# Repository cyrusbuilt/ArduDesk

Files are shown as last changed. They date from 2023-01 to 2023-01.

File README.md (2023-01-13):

# ArduDesk
Arduino (ESP8266-based) IoT Desk Controller

## What is it?

ArduDesk is an "intelligent" desk controller designed to work with [Uplift V2 standing desks](https://www.upliftdesk.com/standing-desks/) and allows for automated control via home-automation systems. This repository contains the firmware, schematics, PCB design files, and OpenHAB integration.

## Why did you make it?

Because why not? Main I just wanted to be able to control my desk from my phone.  The buttonpad that came with my desk allows raising/lowering and nothing else. No presets or anything. I quickly realized that I wanted to be able to just hit a button to go to a preset height for when I'm sitting and another for when I want to stand. ArduDesk fills those requirements and then some.

## But like... you can order a replacement handset that does that.

You are correct. Uplift does indeed make [varying different control pads that can do that](https://www.upliftdesk.com/advanced-comfort-flush-keypad-by-uplift-desk/) and they even make a [bluetooth adapter](https://www.upliftdesk.com/bluetooth-adapter-for-uplift-desk/). But I wanted to integrate with the rest of my home automation ecosystem, which opens up a bunch of other possibilities.

## So how does it work?

ArduDesk is designed to be a man-in-the-middle device. Meaning, can continue to use your existing button pad *and* ArduDesk due to ArduDesk's passthrough circuitry. The idea is you simply unplug your existing button pad from the desk's control box, and plug it into ArduDesk instead. Then take a regular network patch cable from ArduDesk to the control box. That is it in terms of connections. ArduDesk get's it's power from the control box and connects to your network over WiFi.

## Ok.. I'm sold. How do I get one?

I don't sell this as a product you can buy or even as a kit. You can grab the gerber files from the 'schematics' folder and send them to a PCB fab house like [PCBWay](https://www.pcbway.com) and have the boards made, then using the Bill-of-Materials (BOM) from the 'schematics' folder you can source the components from places like [DigiKey](https://www.digikey.com) and then whip out your soldering iron and assemble the board yourself. Some fab houses also offer to assemble the boards for you for an added fee.

## I have an assembled board, now what?

You'll need an FTDI cable like [this one](https://www.adafruit.com/product/70). Connect the USB end to your computer and the other end to the programming/monitoring header on ArduDesk board then press both buttons on the ESP8266 breakout module to put it into programming mode. Modify the config.json file in the 'data' folder to meet your needs. You may also need to modify the monitor_port setting in platformio.ini file to point to the correct serial port for your FTDI cable. If you don't already have [PlatformIO](https://platformio.org/) installed, you'll need to do that next (make sure if installed the VSCode extension, you also install the command line utils). Then you can run:

```shell
> pio run --environment huzzah --target uploadfs
```

and wait for it to complete. When it's done, press the reset button quickly followed by pressing both buttons to put it back in programming mode again. Then run:

```shell
> pio run --environment huzzah --target upload --target monitor
```

and wait for it to complete. Then press the reset button again and ArduDesk should start booting up. You should still be able to control your desk using the existing button pad. But now you can also control via [MQTT](https://mqtt.org/) or any software that allows integration via MQTT.

## The Nitty Gritty
Once every 5 seconds (by default), ArduDesk will poll the current state and height values and publish a status payload to the configured MQTT status topic. Likewise, you can send a control payload the configured MQTT control topic to raise or lower the height and stop the desk while it's actively moving. Now let's get deeper into details...

## Project Structure
This is a PlatformIO project, so please refer to the PlatformIO documentation for building.

```
|-- .github          # Continuous integration stuff
|-- data             # Configuration data. Anything here gets flashed when uploading a filesystem image
|-- include          # Contains C++ header files for the firmware
|-- openhab          # Contains OpenHAB integration files
|-- schematics       # Contains schematics (EasyEDA and PDF), PCB design (EasyEDA and PDF), BoM, and gerbers
|-- src              # Contains C++ sources for the firmware
|-- LICENSE          # MIT open source license
|-- platformio.ini   # PlatformIO project configuration file
|-- README.md        # This file
```

# Configuration

The config.h file contains default configuration directives. These options are the hardcoded default values that the system will initially boot with. However, if there is a config.json file present in the root of the SPIFFS file system, then its values will override the defaults. Here we'll discuss each option:

- DEBUG: Uncomment this define to generate additional debug output in the console.
- ENABLE_OTA: If you do not wish to support OTA updates, just comment this define.
- ENABLE_MDNS: If you do not wish to support [MDNS](https://tttapa.github.io/ESP8266/Chap08%20-%20mDNS.html), comment this define.
- CONFIG_FILE_PATH: This is the path to the configuration file. The default is /config.json. The values in this file will override these defaults.
- DEFAULT_SSID: Change this line to reflect the SSID of your WiFi network.
- DEFAULT_PASSWORD: Change this line to reflect the password to your WiFi network.
- CLOCK_TIMEZONE: The GMT offset for your timezone (EST [America/New York] is -4 when observing DST. It's -5 when not).
- SERIAL_BAUD: While it is not recommended, you can change the BAUD rate of the serial port here.
- CHECK_WIFI_INTERVAL: The interval (in milliseconds) to check the water depth.
- CLOCK_SYNC_INTERVAL: The interval (in milliseconds) to try to resync the clock with NTP. Default is 1 hour.
- CHECK_DESK_HEIGHT_INTERVAL: The interval (in milliseconds) to get the desk height and state and publish if there has been a change since the last check.
- DEVICE_NAME: This essentially serves as the host name of the device on the network (default is ARDUDESK).
- CHECK_MQTT_INTERVAL: The interval (in milliseconds) to check connectivity to the MQTT broker. If the connection is lost, a reconnect will occur. The default value is 5 minutes.
- MQTT_TOPIC_STATUS: The MQTT status topic to publish device status messages to. Default is 'ardudesk/status'.
- MQTT_TOPIC_CONTROL: The MQTT control topic to subscribe to for control messages. Default is 'ardudesk/control'.
- MQTT_TOPIC_DISCOVERY: The MQTT discovery topic to publish discovery payloads to for systems that support device discovery via MQTT (specifically, [RedQueen](https://github.com/cyrusbuilt/RedQueen)).
- MQTT_BROKER: The hostname or IP of the MQTT broker.
- MQTT_PORT: The port on the MQTT broker to connect to. The default is 1883.
- OTA_HOST_PORT: Defines the port to listen for OTA updates on. This option is ignored if ENABLE_OTA is disabled.
- OTA_PASSWORD: The password used to authenticate with the OTA server. This option is ignored if ENABLE_OTA is disabled.
- defaultIp: The default IP address. By default, this device boots with a static IP configuration. The default IP is 192.168.0.229. You can change that here if you wish, but ideally you would just change it in config.json instead.
- defaultGw: The default gateway. The current default is 192.168.0.1. You can change that here if you wish.
- defaultSm: The subnet mask. By default, it is 255.255.255.0, but you can change that here if need be.
- defaultDns: The default primary DNS server. The current default is the same as the gateway (the typical configuration for residential routers) which is 192.168.0.1. You can change that here if you wish.

To override the default configuration options, you need to upload the 'config.json' file in the 'data' folder modified with your desired values. The file should look something like this:

```json
{
	"hostname": "ARDUDESK",
	"useDHCP": false,
	"ip": "192.168.0.229",
	"gateway": "192.168.0.1",
	"subnetMask": "255.255.255.0",
	"dnsServer": "192.168.0.1",
	"wifiSSID": "your_ssid_here",
	"wifiPassword": "your_wifi_password_here",
	"otaPort": 8266,
	"otaPassword": "your_ota_password_here",
	"mqttBroker": "your_mqtt_broker",
	"mqttPort": 1883,
	"mqttControlTopic": "ardudesk/control",
	"mqttStatusTopic": "ardudesk/status",
	"mqttUsername": "your_mqtt_username",
	"mqttPassword": "your_mqtt_password",
	"sittingHeight": 30,
	"standingHeight": 231
}
```

This configuration file is pretty self-explanatory. The file *MUST* be located in the 'data' directory located in the root of the project in order to be picked up by the flash uploader (either via Serial or OTA). Each of the options in the configuration file match up with the hard-coded default settings mentioned above. If this file is not present when the firmware boots, a new file will be created and populated with the hard-coded defaults. These defaults can then be changed via the fail-safe menu and saved. You'll notice some additonal options in the config.json file not present in config.h. They are as follows:

- mqttUsername: If you have enabled password authentication on your MQTT broker, provide the username here.
- mqttPassword: If you have enabled password authentication on your MQTT borker, provide the password here.
- sittingHeight: The desired height value for when you are sitting (0 - 256).
- standingHeight: The desired height value for when you are standing (0 - 256).

## OTA Updates
If you wish to be able to upload firmware updates Over-the-Air, then besides leaving the ENABLE_OTA option uncommented, you will also need to uncomment all the upload_* lines in platformio.ini, and change the line 'upload_port = ' to reflect the IP of the device and the line '--auth=' to reflect whatever 'otaPassword' in config.json is set to. Then when you click "upload" from the PlatformIO tasks (or if you execute 'pio run --target upload' from the command line) it should upload directly over WiFi and once completed, the device will automatically flash itself and reboot with the new version. If you wish to upload a new configuration file, you can also do this via OTA. Assuming the above-mentioned settings are configured, you can then click "Upload File System Image" from the PlatformIO project tasks (or execute 'pio run --target uploadfs' from the command line).

## Serial Console

If the device ever fails to connect to WiFi or if you press the 'i' key on your keyboard while in the serial console, normal operation of the device is suspended and the device will fall into a 'fail-safe' mode and present the user with a command menu, which can be used to reconfigure the device, reboot, or manually control the desk, etc.

## Integration

As previously mentioned, this was intended to be integrated with 3rd-party systems (ie. Home Automation). While my personal preference is [OpenHAB](https://www.openhab.org/), since ArduDesk communicates over MQTT, it can be integrated with any other system that can use MQTT as well (ie. [Home Assistant](https://www.home-assistant.io/), [Node-RED](https://nodered.org/), etc). While the integration files included in this repo are for OpenHAB, you should be able to fairly easily create your own configuration files to integrate with other systems. Do do so, you'll need the JSON message schema below:

ArduDesk control schema (refer to the ControlCommand enum in TelemetryHelper.h for valid command values):
```json
{
	"type": "object",
	"required": ["clientId", "command"],'
	"properties": {
		"clientId": {
			"type": "string"
		},
		"command": {
			"type": "integer",
			"minimum": 0,
			"maximum": 7
		},
		"requestedHeight": {
			"type": "integer",
			"minimum": 0,
			"maximum": 256
		}
	}
}
```

Example 1: Stand (Move to standing height preset)
```json
{
	"clientId": "ARDUDESK",
	"command": 7
}
```

Example 2: Move to specified height value (180 for this example)
```json
{
	"clientId": "ARDUDESK",
	"command": 4,
	"requestedHeight": 180
}
```

ArduDesk Status Schema (refer to SystemState enum in TelemetryHelper.h for valid system state values):
```json
{
	"type": "object",
	"required": [
		"clientId",
		"firmwareVersion",
		"systemState",
		"height",
		"state"
	],
	"properties": {
		"clientId": {
			"type": "string"
		},
		"firmwareVersion": {
			"type": "string"
		},
		"systemState": {
			"type": "integer",
			"minimum": 0,
			"maximum": 3
		},
		"height": {
			"type": "integer",
			"minimum": 0,
			"maximum": 256
		},
		"state": {
			"type": string
		},
		"sittingHeight": {
			"type": "integer",
			"minimum": 0,
			"maximum": 256
		},
		"standingHeight": {
			"type": "integer",
			"minimum": 0,
			"maximum": 256
		}
	}
}
```

Example (normal operation, desk idle at requested height):
```json
{
	"clientId": "ARDUDESK",
	"firmwareVersion": "1.1",
	"systemState": 1,
	"height": 180,
	"state": "STOPPED",
	"sittingHeight": 31,
	"standingHeight": 230
}
```

An ArduDesk status payload is emitted to the status topic periodically and every time there is a status change.

ArduDesk Discovery Schema:
```json
{
	"type": "object",
	"required": ["name", "class", "statusTopic", "controlTopic"],
	"properties": {
		"name": {
			"type": "string"
		},
		"class": {
			"type": "string"
		},
		"statusTopic": {
			"type": "string"
		},
		"controlTopic": {
			"type": "string"
		}
	}
}
```

Example:
```json
{
	"name": "ARDUDESK",
	"class": "ADUDESK",
	"statusTopic": "ardudesk/status",
	"controlTopic": "ardudesk/control"
}
```

An ArduDesk Discovery payload is emitted periodically whenever the MQTT connection check occurs.

## Interfacing With Uplift Desk
Based on everything I've read, examples I've seen, and my own experimentation, Uplift V2 desks appear to follow the same protocol over RS-232 Serial as [Jarvis](https://www.fully.com/standing-desks.html).

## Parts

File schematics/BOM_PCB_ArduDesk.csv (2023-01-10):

ID | Name | Designator | Footprint | Quantity | Manufacturer Part | Manufacturer | Supplier | Supplier Part | Price
1 | FRJ45007-1100K6K02B0 | RJ1,RJ2 | RJ45-TH_FRJ45007-1100K6K02B0 | 2 | FRJ45007-1100K6K02B0 | TXGA(特思嘉) | LCSC | C2834418 | 0.528
2 | ADAFRUIT HUZZAH ESP8266 BREAKOUT | U1 | HUZZAH 8266 | 1 |  | Adafruit
3 | LED 5MM GREEN | D1 | LED 5MM GREEN | 1
4 | 5mm | D2 | PKG-LED-5MM-RED | 1 | L-1503EC | KINGBRIGHT | Element14 | 1003201
5 | HEADER 1X6 | H1 | HEADER-1X6-2.54MM | 1
6 | 2N7000 | Q1,Q2,Q3,Q4,Q5,Q6 | 2N7000 TO-92 B | 6
7 | Resistor_10K_Ohm | R1,R2,R3,R4,R5,R6,R7,R8,R9,R10,R11,R12 | RESISTOR_10KOHM | 12
8 | 150 | R13 | PKG-0.25W RESISTOR | 1 | MCF 0.25W 150R | MULTICOMP | Element14 | 9339175

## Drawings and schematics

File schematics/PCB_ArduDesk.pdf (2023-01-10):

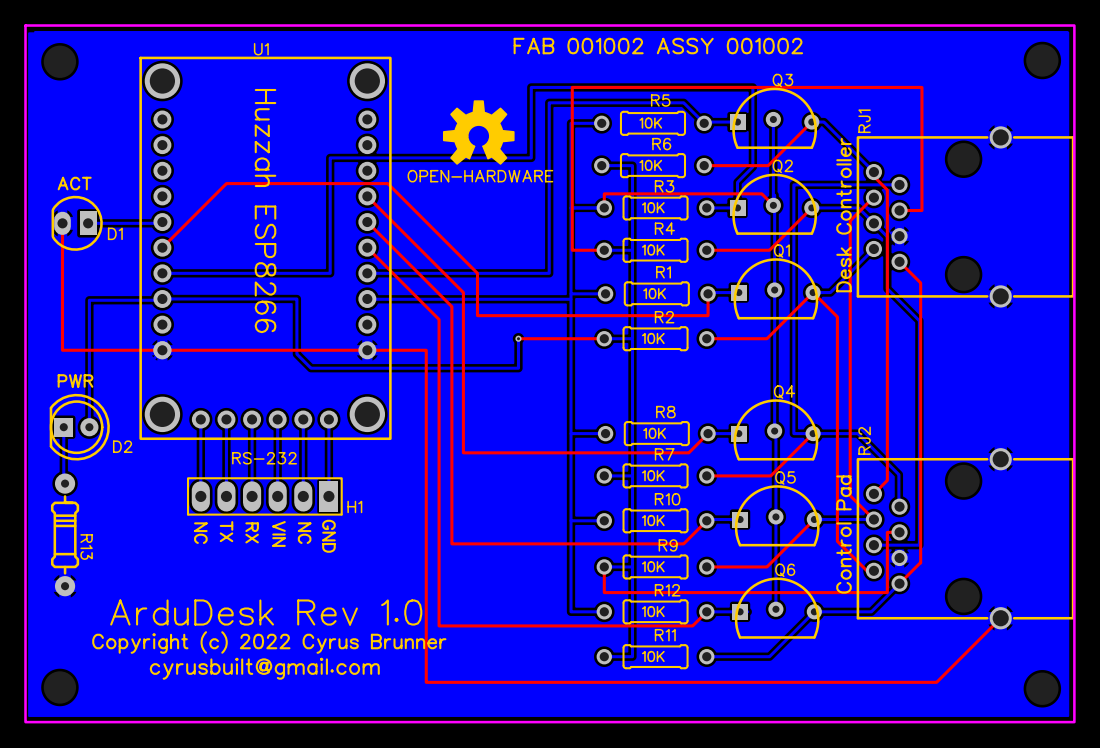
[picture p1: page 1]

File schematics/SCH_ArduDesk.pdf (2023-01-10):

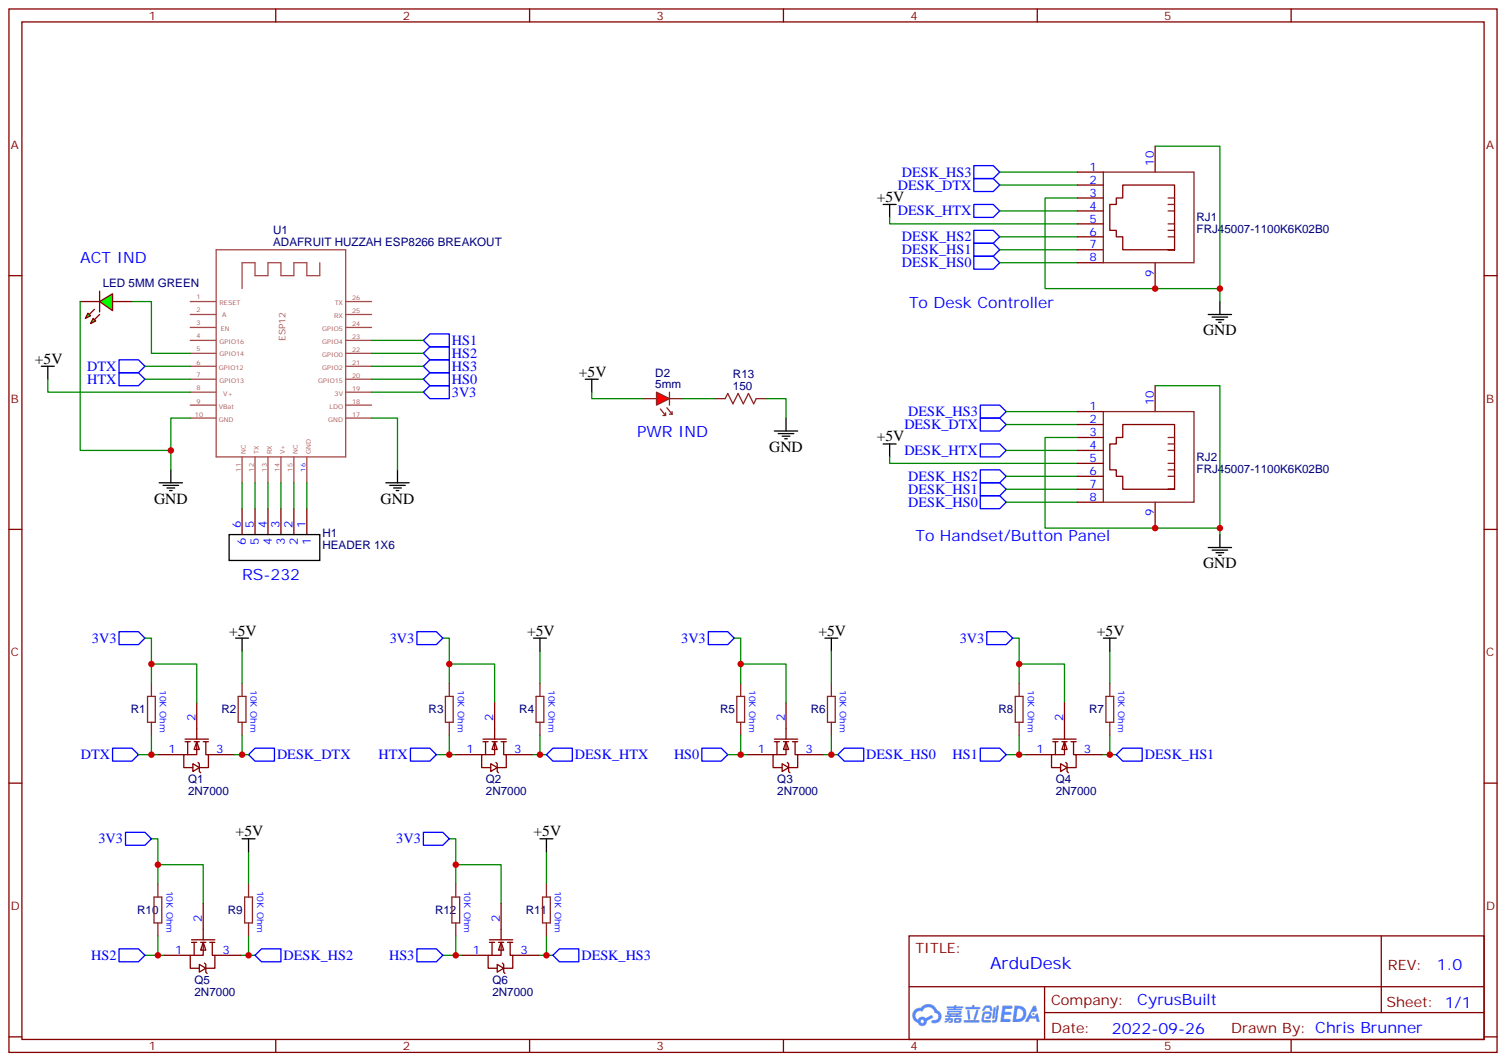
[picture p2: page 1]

Drawn By: Chris Brunner

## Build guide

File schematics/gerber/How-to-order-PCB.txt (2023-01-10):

How to Order PCB

Please refer to:
https://docs.easyeda.com/en/PCB/Order-PCB

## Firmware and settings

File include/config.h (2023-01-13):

#ifndef _CONFIG_H
#define _CONFIG_H

#include <IPAddress.h>

//#define DEBUG                                       // Comment to disable debug output.
#define DEVICE_NAME "ARDUDESK"		                // The device name (hostname).
#define DEVICE_CLASS "ardudesk"                     // The device class (used for discovery).
#define BAUD_RATE 115200                            // The BAUD rate (speed) of the serial port (console).
#define ENABLE_OTA                                  // Comment to disable OTA (over-the-air) firmware updates.
#define ENABLE_MDNS                                 // Comment to disable MDNS (multicast-DNS) support.
#define CONFIG_FILE_PATH "/config.json"             // Config file path. Do not alter unless you are sure.
#define DEFAULT_SSID "your_ssid_here"               // Put the SSID of your WiFi here.
#define DEFAULT_PASSWORD "your_wifi_password"       // Put your WiFi password here.
#define CLOCK_TIMEZONE -4                           // The timezone this device is located in. (For example, EST when observing DST = GMT -4, when not = GMT -5).
#define CHECK_WIFI_INTERVAL 30000                   // How often to check WiFi status (millis)
#define CLOCK_SYNC_INTERVAL 3600000                 // How often to sync the local clock with NTP (millis)
#define CHECK_DESK_HEIGHT_INTERVAL 5000             // How often to chec the sensors.
#define CHECK_MQTT_INTERVAL 60000 * 5               // MQTT connectivity check interval (millis).
#define MQTT_TOPIC_STATUS "ardudesk/status"     	// MQTT status channel to publish to.
#define MQTT_TOPIC_CONTROL "ardudesk/control"   	// MQTT control channel to subscribe to.
#define MQTT_TOPIC_DISCOVERY "redqueen/config"      // MQTT discovery topic to publish to.
#define MQTT_BROKER "your_mqtt_broker_ip"           // MQTT broker hostname or IP.
#define MQTT_PORT 1883                              // MQTT port number.
#ifdef ENABLE_OTA
    #include <ArduinoOTA.h>
    #define OTA_HOST_PORT 8266                      // The OTA updater port.
    #define OTA_PASSWORD "your_ota_password_here"   // The OTA updater password.
#endif
const IPAddress defaultIp(192, 168, 0, 229);        // Default static IP address.
const IPAddress defaultGw(192, 168, 0, 1);          // Default static gateway address.
const IPAddress defaultSm(255, 255, 255, 0);        // Default static subnet mask.
const IPAddress defaultDns(192, 168, 0, 1);         // Default static primary DNS address.

typedef struct {
    // Network stuff
    String hostname;
    String ssid;
    String password;
    IPAddress ip;
    IPAddress gw;
    IPAddress sm;
    IPAddress dns;
    bool useDhcp;

    uint8_t clockTimezone;

    // MQTT stuff
    String mqttTopicStatus;
    String mqttTopicControl;
    String mqttTopicDiscovery;
    String mqttBroker;
    String mqttUsername;
    String mqttPassword;
    uint16_t mqttPort;

    // OTA stuff
    uint16_t otaPort;
    String otaPassword;

    // Desk height presets
    int16_t sittingHeight;
    int16_t standingHeight;
} config_t;

#endif

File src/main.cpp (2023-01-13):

/**
 * @file main.cpp
 * @author Cyrus Brunner (cyrusbuilt at gmail dot com)
 * @brief Firmware for ArduDesk.
 * @version 1.1
 * @date 2022-09-29
 * 
 * @copyright Copyright (c) 2022 Cyrus Brunner
 * 
 */

#ifndef ESP8266
    #error This firmware is only compatible with ESP8266 controllers.
#endif

#include <Arduino.h>
#include <FS.h>
#include <time.h>
#include <TZ.h>
#include <Wire.h>
#include "ArduinoJson.h"
#include "ESPCrashMonitor.h"
#include "Console.h"
#include "LED.h"
#include "PubSubClient.h"
#include "ResetManager.h"
#include "SoftwareSerial.h"
#include "TaskScheduler.h"
#include "TelemetryHelper.h"
#include "config.h"
#include "UpliftDesk.h"

#define FIRMWARE_VERSION "1.1"

// Pin definitions
#define PIN_WIFI_LED 14

// From https://github.com/phord/Jarvis
// Pin 	Label 	Description
// 1  	HS3 	Handset control line 3 [1]
// 2 	TX 	    Serial control messages from controller to handset [2]
// 3 	GND 	Ground
// 4 	RX   	Serial control messages from handset to controller [2]
// 5 	VCC 	Vcc (5vdc) supply from desk controller [3]
// 6 	HS2 	Handset control line 2 [1]
// 7 	HS1 	Handset control line 1 [1]
// 8 	HS0 	Handset control line 0 [1]
#define PIN_DTX 12
#define PIN_HTX 13
#define PIN_HS0 15
#define PIN_HS1 4
#define PIN_HS2 0
#define PIN_HS3 2

// Forward declarations
void onCheckWifi();
void onCheckMqtt();
void onSyncClock();
void onReadHeight();
void onMqttMessage(char* topic, byte* payload, unsigned int length);

// Global vars.
#ifdef ENABLE_MDNS
    #include <ESP8266mDNS.h>
    MDNSResponder mdns;
#endif
WiFiClient wifiClient;
PubSubClient mqttClient(wifiClient);
Task tCheckWiFi(CHECK_WIFI_INTERVAL, TASK_FOREVER, &onCheckWifi);
Task tCheckMqtt(CHECK_MQTT_INTERVAL, TASK_FOREVER, &onCheckMqtt);
Task tClockSync(CLOCK_SYNC_INTERVAL, TASK_FOREVER, &onSyncClock);
Task tReadHeight(CHECK_DESK_HEIGHT_INTERVAL, TASK_FOREVER, &onReadHeight);
Scheduler taskMan;
LED wifiLED(PIN_WIFI_LED, NULL);
config_t config;
bool filesystemMounted = false;
int16_t requestedHeight = 0;
int16_t lastHeight = 0;
volatile SystemState sysState = SystemState::BOOTING;

/**
 * @brief Get the current date/time as string (adjusted for local time and DST).
 * 
 * @return String The current time string.
 */
String getTimeInfo() {
    time_t now = time(nullptr);
    struct tm *timeinfo = localtime(&now);
    String result = String(asctime(timeinfo));
    result.replace("\n", "");
    return result;
}

/**
 * @brief Synchronize the local system clock via NTP. Note: This does not take DST
 * into account. Currently, you will have to adjust the CLOCK_TIMEZONE define
 * manually to account for DST when needed.
 */
void onSyncClock() {
    wifiLED.on();
    // TODO Support configurable time zones.
    configTzTime(TZ_America_New_York, "pool.ntp.org");

    Serial.print("INIT: Waiting for NTP time sync...");
    delay(500);
    while (!time(nullptr)) {
        wifiLED.off();
        ESPCrashMonitor.iAmAlive();
        Serial.print(F("."));
        delay(500);
        wifiLED.on();
    }
    
    wifiLED.off();
    Serial.println(F(" DONE"));
    Serial.print(F("INFO: Current time: "));
    Serial.println(getTimeInfo());
}

/**
 * @brief Publishes the current system status as a JSON payload to the MQTT
 * status topic, if connected. This will also flash the WiFi activity LED.
 */
void publishSystemState() {
    if (mqttClient.connected()) {
        wifiLED.on();

        DynamicJsonDocument doc(250);
        doc["clientId"] = config.hostname.c_str();
        doc["firmwareVersion"] = FIRMWARE_VERSION;
        doc["systemState"] = (uint8_t)sysState;
        doc["height"] = UpliftDesk.getHeight();
        doc["state"] = UpliftDesk.getStateString();
        doc["sittingHeight"] = config.sittingHeight;
        doc["standingHeight"] = config.standingHeight;
		
        String jsonStr;
        size_t len = serializeJson(doc, jsonStr);
        Serial.print(F("INFO: Publishing system state: "));
        Serial.println(jsonStr);
        if (!mqttClient.publish(config.mqttTopicStatus.c_str(), jsonStr.c_str(), len)) {
            Serial.println(F("ERROR: Failed to publish message."));
        }

        doc.clear();
        wifiLED.off();
    }
}

/**
 * @brief Publishes a device discovery packet to the configured discovery topic.
 */
void publishDiscoveryPacket() {
    if (mqttClient.connected()) {
        wifiLED.on();

        DynamicJsonDocument doc(250);
        doc["name"] = config.hostname;
        doc["class"] = DEVICE_CLASS;
        doc["statusTopic"] = config.mqttTopicStatus;
        doc["controlTopic"] = config.mqttTopicControl;

        String jsonStr;
        size_t len = serializeJson(doc, jsonStr);
        Serial.print(F("INFO: Publishing discovery packet: "));
        Serial.println(jsonStr);
        if (!mqttClient.publish(config.mqttTopicDiscovery.c_str(), jsonStr.c_str(), len)) {
            Serial.println(F("ERROR: Failed to publish message."));
        }

        doc.clear();
        wifiLED.off();
    }
}

/**
 * @brief Task handler that reads the current desk height and if it differs
 * from the last time it was read, will publish the new height.
 */
void onReadHeight() {
	Serial.println(F("INFO: Reading desk height ..."));
	int16_t currentHeight = UpliftDesk.getHeight();
    if (currentHeight != lastHeight) {
        publishSystemState();
    }

    lastHeight = currentHeight;
}

/**
 * @brief Resume normal operation. This will resume any suspended tasks.
 */
void resumeNormal() {
    Serial.println(F("INFO: Resuming normal operation..."));
    taskMan.enableAll();
    wifiLED.off();
    sysState = SystemState::NORMAL;
    publishSystemState();
}

/**
 * @brief Prints network information details to the serial console.
 */
void printNetworkInfo() {
    Serial.print(F("INFO: Local IP: "));
    Serial.println(WiFi.localIP());
    Serial.print(F("INFO: Gateway: "));
    Serial.println(WiFi.gatewayIP());
    Serial.print(F("INFO: Subnet mask: "));
    Serial.println(WiFi.subnetMask());
    Serial.print(F("INFO: DNS server: "));
    Serial.println(WiFi.dnsIP());
    Serial.print(F("INFO: MAC address: "));
    Serial.println(WiFi.macAddress());
    #ifdef DEBUG
        WiFi.printDiag(Serial);
    #endif
}

/**
 * @brief Performs a soft-restart of the system.
 */
void reboot() {
    Serial.println(F("INFO: Rebooting..."));
    Serial.flush();
    delay(1000);
    ResetManager.softReset();
}

/**
 * @brief Saves the configuration data to the config file.
 */
void saveConfiguration() {
    Serial.print(F("INFO: Saving configuration to "));
    Serial.print(CONFIG_FILE_PATH);
    Serial.println(F(" ... "));
    if (!filesystemMounted) {
        Serial.println(F("FAIL"));
        Serial.println(F("ERROR: Filesystem not mounted."));
        return;
    }

    StaticJsonDocument<400> doc;
    doc["hostname"] = config.hostname;
    doc["useDhcp"] = config.useDhcp;
    IPAddress ipAddr = IPAddress(config.ip);
    doc["ip"] = ipAddr.toString();
    ipAddr = IPAddress(config.gw);
    doc["gateway"] = ipAddr.toString();
    ipAddr = IPAddress(config.sm);
    doc["subnetmask"] = ipAddr.toString();
    ipAddr = IPAddress(config.dns);
    doc["dnsServer"] = ipAddr.toString();
    doc["wifiSSID"] = config.ssid;
    doc["wifiPassword"] = config.password;
    doc["timezone"] = config.clockTimezone;
    doc["mqttBroker"] = config.mqttBroker;
    doc["mqttPort"] = config.mqttPort;
    doc["mqttControlTopic"] = config.mqttTopicControl;
    doc["mqttStatusTopic"] = config.mqttTopicStatus;
    doc["mqttDiscoveryTopic"] = config.mqttTopicDiscovery;
    doc["mqttUsername"] = config.mqttUsername;
    doc["mqttPassword"] = config.mqttPassword;
    doc["sittingHeight"] = config.sittingHeight;
    doc["standingHeight"] = config.standingHeight;
    #ifdef ENABLE_OTA
        doc["otaPort"] = config.otaPort;
        doc["otaPassword"] = config.otaPassword;
    #endif

    File configFile = SPIFFS.open(CONFIG_FILE_PATH, "w");
    if (!configFile) {
        Serial.println(F("FAIL"));
        Serial.println(F("ERROR: Failed to open config file for writing."));
        doc.clear();
        return;
    }

    serializeJsonPretty(doc, configFile);
    doc.clear();
    configFile.flush();
    configFile.close();
    Serial.println(F("DONE"));
}

/**
 * @brief Helper method for printing warnings about configuration settings.
 * 
 * @param message The warning message to print.
 */
void printWarningAndContinue(const __FlashStringHelper *message) {
    Serial.println();
    Serial.println(message);
    Serial.print(F("INFO: Continuing... "));
}

/**
 * @brief Sets all the configuration values to their defaults.
 */
void setConfigurationDefaults() {
    String chipId = String(ESP.getChipId(), HEX);
    String defHostname = String(DEVICE_NAME) + "_" + chipId;

    config.hostname = defHostname;
    config.ip = defaultIp;
    config.mqttBroker = MQTT_BROKER;
    config.mqttPassword = "";
    config.mqttPort = MQTT_PORT;
    config.mqttTopicControl = MQTT_TOPIC_CONTROL;
    config.mqttTopicStatus = MQTT_TOPIC_STATUS;
    config.mqttTopicDiscovery = MQTT_TOPIC_DISCOVERY;
    config.mqttUsername = "";
    config.password = DEFAULT_PASSWORD;
    config.sm = defaultSm;
    config.ssid = DEFAULT_SSID;
    config.useDhcp = false;
    config.clockTimezone = CLOCK_TIMEZONE;
    config.dns = defaultDns;
    config.gw = defaultGw;
    config.sittingHeight = 0;
    config.standingHeight = 0;

    #ifdef ENABLE_OTA
        config.otaPassword = OTA_PASSWORD;
        config.otaPort = OTA_HOST_PORT;
    #endif
}

/**
 * @brief Loads the configuration parameters into memory, defaulting the
 * configuration values where necessary.
 */
void loadConfiguration() {
    memset(&config, 0, sizeof(config));

    Serial.print(F("INFO: Loading config file "));
    Serial.print(CONFIG_FILE_PATH);
    Serial.print(F(" ... "));
    if (!filesystemMounted) {
        Serial.println(F("FAIL"));
        Serial.println(F("ERROR: Filesystem not mounted."));
        return;
    }

    if (!SPIFFS.exists(CONFIG_FILE_PATH)) {
        Serial.println(F("FAIL"));
        Serial.println(F("WARN: Config file does not exist. Creating with default config ..."));
        saveConfiguration();
        return;
    }

    File configFile = SPIFFS.open(CONFIG_FILE_PATH, "r");
    if (!configFile) {
        Serial.println(F("FAIL"));
        Serial.println(F("ERROR: Unable to open config file. Using default config."));
        return;
    }

    size_t size = configFile.size();
    uint16_t freeMem = ESP.getMaxFreeBlockSize() - 512;
    if (size > freeMem) {
        Serial.println(F("FAIL"));
        Serial.print(F("ERROR: Not enough free memory to load document. Size = "));
        Serial.print(size);
        Serial.print(F(", Free = "));
        Serial.println(freeMem);
        configFile.close();
        return;
    }

    DynamicJsonDocument doc(freeMem);
    DeserializationError error = deserializeJson(doc, configFile);
    if (error) {
        Serial.println(F("FAIL"));
        Serial.println(F("ERROR: Fail to parse config file to JSON. Using default config."));
        configFile.close();
        return;
    }

    doc.shrinkToFit();
    configFile.close();

    String chipId = String(ESP.getChipId(), HEX);
    String defHostname = String(DEVICE_NAME) + "_" + chipId;

    config.hostname = doc.containsKey("hostname") ? doc["hostname"].as<String>() : defHostname;
    config.useDhcp = doc.containsKey("isDhcp") ? doc["isDhcp"].as<bool>() : false;
    
    if (doc.containsKey("ip")) {
        if (!config.ip.fromString(doc["ip"].as<String>())) {
            printWarningAndContinue(F("WARN: Invalid IP in configuration. Falling back to factory default."));
        }
    }
    else {
        config.ip = defaultIp;
    }

    if (doc.containsKey("gateway")) {
        if (!config.gw.fromString(doc["gateway"].as<String>())) {
            printWarningAndContinue(F("WARN: Invalid gateway in configuration. Falling back to factory default."));
        }
    }
    else {
        config.gw = defaultGw;
    }

    if (doc.containsKey("subnetmask")) {
        if (!config.sm.fromString(doc["subnetmask"].as<String>())) {
            printWarningAndContinue(F("WARN: Invalid subnet mask in configuration. Falling back to factory default."));
        }
    }
    else {
        config.sm = defaultSm;
    }

    if (doc.containsKey("dns")) {
        if (!config.dns.fromString(doc["dns"].as<String>())) {
            printWarningAndContinue(F("WARN: Invalid DNS IP in configuration. Falling back to factory default."));
        }
    }
    else {
        config.dns = defaultDns;
    }

    config.ssid = doc.containsKey("wifiSSID") ? doc["wifiSSID"].as<String>() : DEFAULT_SSID;
    config.password = doc.containsKey("wifiPassword") ? doc["wifiPassword"].as<String>() : DEFAULT_PASSWORD;
    config.clockTimezone = doc.containsKey("timezone") ? doc["timezone"].as<uint8_t>() : CLOCK_TIMEZONE;
    config.mqttBroker = doc.containsKey("mqttBroker") ? doc["mqttBroker"].as<String>() : MQTT_BROKER;
    config.mqttPort = doc.containsKey("mqttPort") ? doc["mqttPort"].as<int>() : MQTT_PORT;
    config.mqttTopicControl = doc.containsKey("mqttControlTopic") ? doc["mqttControlTopic"].as<String>() : MQTT_TOPIC_CONTROL;
    config.mqttTopicStatus = doc.containsKey("mqttStatusTopic") ? doc["mqttStatusTopic"].as<String>() : MQTT_TOPIC_STATUS;
    config.mqttTopicDiscovery = doc.containsKey("mqttDiscoveryTopic") ? doc["mqttDiscoveryTopic"].as<String>() : MQTT_TOPIC_DISCOVERY;
    config.mqttUsername = doc.containsKey("mqttUsername") ? doc["mqttUsername"].as<String>() : "";
    config.mqttPassword = doc.containsKey("mqttPassword") ? doc["mqttPassword"].as<String>() : "";
    config.sittingHeight = doc.containsKey("sittingHeight") ? doc["sittingHeight"].as<int16_t>() : 0;
    config.standingHeight = doc.containsKey("standingHeight") ? doc["standingHeight"].as<int16_t>() : 0;

    #ifdef ENABLE_OTA
        config.otaPort = doc.containsKey("otaPort") ? doc["otaPort"].as<uint16_t>() : MQTT_PORT;
        config.otaPassword = doc.containsKey("otaPassword") ? doc["otaPassword"].as<String>() : OTA_PASSWORD;
    #endif

    doc.clear();
    Serial.println(F("DONE"));
}

/**
 * @brief Performs a "factory restore" of the configuration data. This clears
 * configuration data on flash and reboots after a 5 second countdown. This
 * will force a configuration file to be generated on restart using default
 * values.
 */
void doFactoryRestore() {
    Serial.println();
    Serial.println(F("Are you sure you wish to restore to factory default? (Y/n)"));
    Console.waitForUserInput();
    
    String str = Console.getInputString();
    if (str == "Y" || str == "y") {
        Serial.print(F("INFO: Clearing current config... "));
        if (filesystemMounted) {
            if (SPIFFS.remove(CONFIG_FILE_PATH)) {
                Serial.println(F("DONE"));
                Serial.print(F("INFO: Removed file: "));
                Serial.println(CONFIG_FILE_PATH);

                Serial.print(F("INFO: Rebooting in "));
                for (uint8_t i = 5; i >= 1; i--) {
                    Serial.print(i);
                    Serial.print(F(" "));
                    delay(1000);
                }

                reboot();
            }
            else {
                Serial.println(F("FAIL"));
                Serial.println(F("ERROR: Failed to delete cofiguration file."));
            }
        }
        else {
            Serial.println(F("FAIL"));
            Serial.println(F("ERROR: Filesystem not mounted."));
        }
    }

    Serial.println();
}

/**
 * @brief Scan for available networks and dump each discovered network to the console.
 */
void getAvailableNetworks() {
    ESPCrashMonitor.defer();
    Serial.println(F("INFO: Scanning WiFi networks..."));
    int numNetworks = WiFi.scanNetworks();
    for (int i = 0; i < numNetworks; i++) {
        Serial.print(F("ID: "));
        Serial.print(i);
        Serial.print(F("\tNetwork name: "));
        Serial.print(WiFi.SSID(i));
        Serial.print(F("\tSignal strength:"));
        Serial.println(WiFi.RSSI(i));
    }
    Serial.println(F("----------------------------------"));
}

/**
 * @brief Reconnect to the MQTT broker and resubscribe to the control topic
 * if no longer connected.
 * 
 * @return true If already connected or successfully reconnected.
 * @return false If no longer connected and unable to reconnect.
 */
bool reconnectMqttClient() {
    if (!mqttClient.connected()) {
        wifiLED.on();
        Serial.print(F("INFO: Attempting to establish MQTT connection to "));
        Serial.print(config.mqttBroker);
        Serial.print(F(" on port "));
        Serial.print(config.mqttPort);
        Serial.println(F(" ... "));

        bool didConnect = false;
        if (config.mqttUsername.length() > 0 && config.mqttPassword.length() > 0) {
            didConnect = mqttClient.connect(config.hostname.c_str(), config.mqttUsername.c_str(), config.mqttPassword.c_str());
        }
        else {
            didConnect = mqttClient.connect(config.hostname.c_str());
        }

        if (didConnect) {
            Serial.print(F("INFO: Subscribing to channel: "));
            Serial.println(config.mqttTopicControl);
            mqttClient.subscribe(config.mqttTopicControl.c_str());

            Serial.print(F("INFO: Publishing to channel: "));
            Serial.println(config.mqttTopicStatus);

            Serial.print(F("INFO: Discovery topic: "));
            Serial.println(config.mqttTopicDiscovery);
        }
        else {
            String failReason = TelemetryHelper::getMqttStateDesc(mqttClient.state());
            Serial.print(F("ERROR: Failed to connect to MQTT broker: "));
            Serial.println(failReason);
            return false;
        }

        wifiLED.off();
    }

    return true;
}

/**
 * @brief Attempts to reconnect to MQTT if necessary and then publishes the
 * current system state. Otherwise, reports the failure.
 */
void onCheckMqtt() {
    Serial.println(F("INFO: Checking MQTT connections status..."));
    if (reconnectMqttClient()) {
        Serial.println(F("INFO: Successfully reconnected to MQTT broker."));
        publishSystemState();
        publishDiscoveryPacket();
    }
    else {
        Serial.println(F("ERROR: MQTT connection lost and reconnect failed."));
        Serial.print(F("INFO: Retrying connection in "));
        Serial.print(CHECK_MQTT_INTERVAL % 1000);
        Serial.println(F(" seconds ..."));
    }
}

/**
 * @brief Movement request handler. If the requested height differs from the
 * current height and the desk is not currently moving, then the desk will
 * move to the requested height and the status will be published.
 */
void handleMoveRequest() {
    if (requestedHeight != UpliftDesk.getHeight() && UpliftDesk.getState() == DeskState::STOPPED) {
        UpliftDesk.goToHeight(requestedHeight);
        publishSystemState();
    }
}

/**
 * @brief Handles control requests recieved from the MQTT control topic and
 * the publishes the current system state. This will execute any valid
 * command it received and ignores any commands that are unrecognized or not
 * valid in the current state.
 * 
 * @param cmd The command to process.
 */
void handleControlRequest(ControlCommand cmd) {
    if (sysState == SystemState::DISABLED && cmd != ControlCommand::ENABLE) {
        // THOU SHALT NOT PASS!!! 
        // We can't process this command because we are disabled.
        Serial.print(F("WARN: Ingoring command "));
        Serial.print((uint8_t)cmd);
        Serial.print(F(" because the system is currently disabled."));
        return;
    }

    switch (cmd) {
        case ControlCommand::ENABLE:
            Serial.println(F("INFO: Enabling system."));
            sysState = SystemState::NORMAL;
            break;
        case ControlCommand::DISABLE:
            Serial.println(F("WARN: Disabling system."));
            sysState = SystemState::DISABLED;
            break;
        case ControlCommand::REBOOT:
            reboot();
            break;
        case ControlCommand::REQUEST_STATUS:
            break;
        case ControlCommand::MOVE:
            handleMoveRequest();
            break;
        case ControlCommand::STOP:
            UpliftDesk.stop();
            break;
        case ControlCommand::SIT:
            requestedHeight = config.sittingHeight;
            handleMoveRequest();
            break;
        case ControlCommand::STAND:
            requestedHeight = config.standingHeight;
            handleMoveRequest();
            break;
        case ControlCommand::SET_SITTING_HEIGHT:
            config.sittingHeight = UpliftDesk.getHeight();
            saveConfiguration();
            break;
        case ControlCommand::SET_STANDING_HEIGHT:
            config.standingHeight = UpliftDesk.getHeight();
            saveConfiguration();
            break;
        default:
            Serial.print(F("WARN: Unknown command: "));
            Serial.println((uint8_t)cmd);
            break;
    }

    publishSystemState();
}
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
void loop() {
	ESPCrashMonitor.iAmAlive();
    Console.checkInterrupt();
    taskMan.execute();
    #ifdef ENABLE_MDNS
        mdns.update();
    #endif
    #ifdef ENABLE_OTA
        ArduinoOTA.handle();
    #endif
    mqttClient.loop();
    UpliftDesk.loop();
}
